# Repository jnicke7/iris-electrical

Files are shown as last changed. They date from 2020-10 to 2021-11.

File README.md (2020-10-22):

# iris-electrical

IRIS Electrical Team Arduino Code Repository

## void setup()

First code run by Arduino on start

Sets up serial inputs for the sabertooth from the Odroid

Assigns the direct and pwm pins as outputs to the LACs

## void loop()

Runs after setup

Creates the checksum to make sure that the data is being passed through to the Arduino correctly

Uses largestOneIndex helper function to calculate

CRC: Cyclic Redundancy Check

If the checksum came out incorrect then it will ignore the instruction.

### Motor ID Values:

    0: Left Drive
    1: Right Drive
    2: Bucket Ladder M
    3: Dump Conveyor LA
    4: Bucket Ladder LA
    5: Agitator
    6: Dump Conveyor M
    7: Shuts off all motors

Based on the motor ID value it will call the sabertooth or the linear actuators

## void linac(int power, int motor)

Inputs: power number and the specific motor number

Outputs: direction and power specific to a motor

Creates changes with two functions:

### digitalWrite(dir\_1, (int)(OdroidIn[1]/128));

Sets the direction of a given motor

### analogWrite(pwm\_3, power\*2);

Sets the magnitude of the given motor

## void stop()

This function runs through each motor and reduces its speed to 0

## int largestOneIndex(unsignedint curr)

This function parses through curr bitwise to find the index of the most significant '1'

Inputs: curr, 16-bit chars

Outputs: integer i, the first index of '1'

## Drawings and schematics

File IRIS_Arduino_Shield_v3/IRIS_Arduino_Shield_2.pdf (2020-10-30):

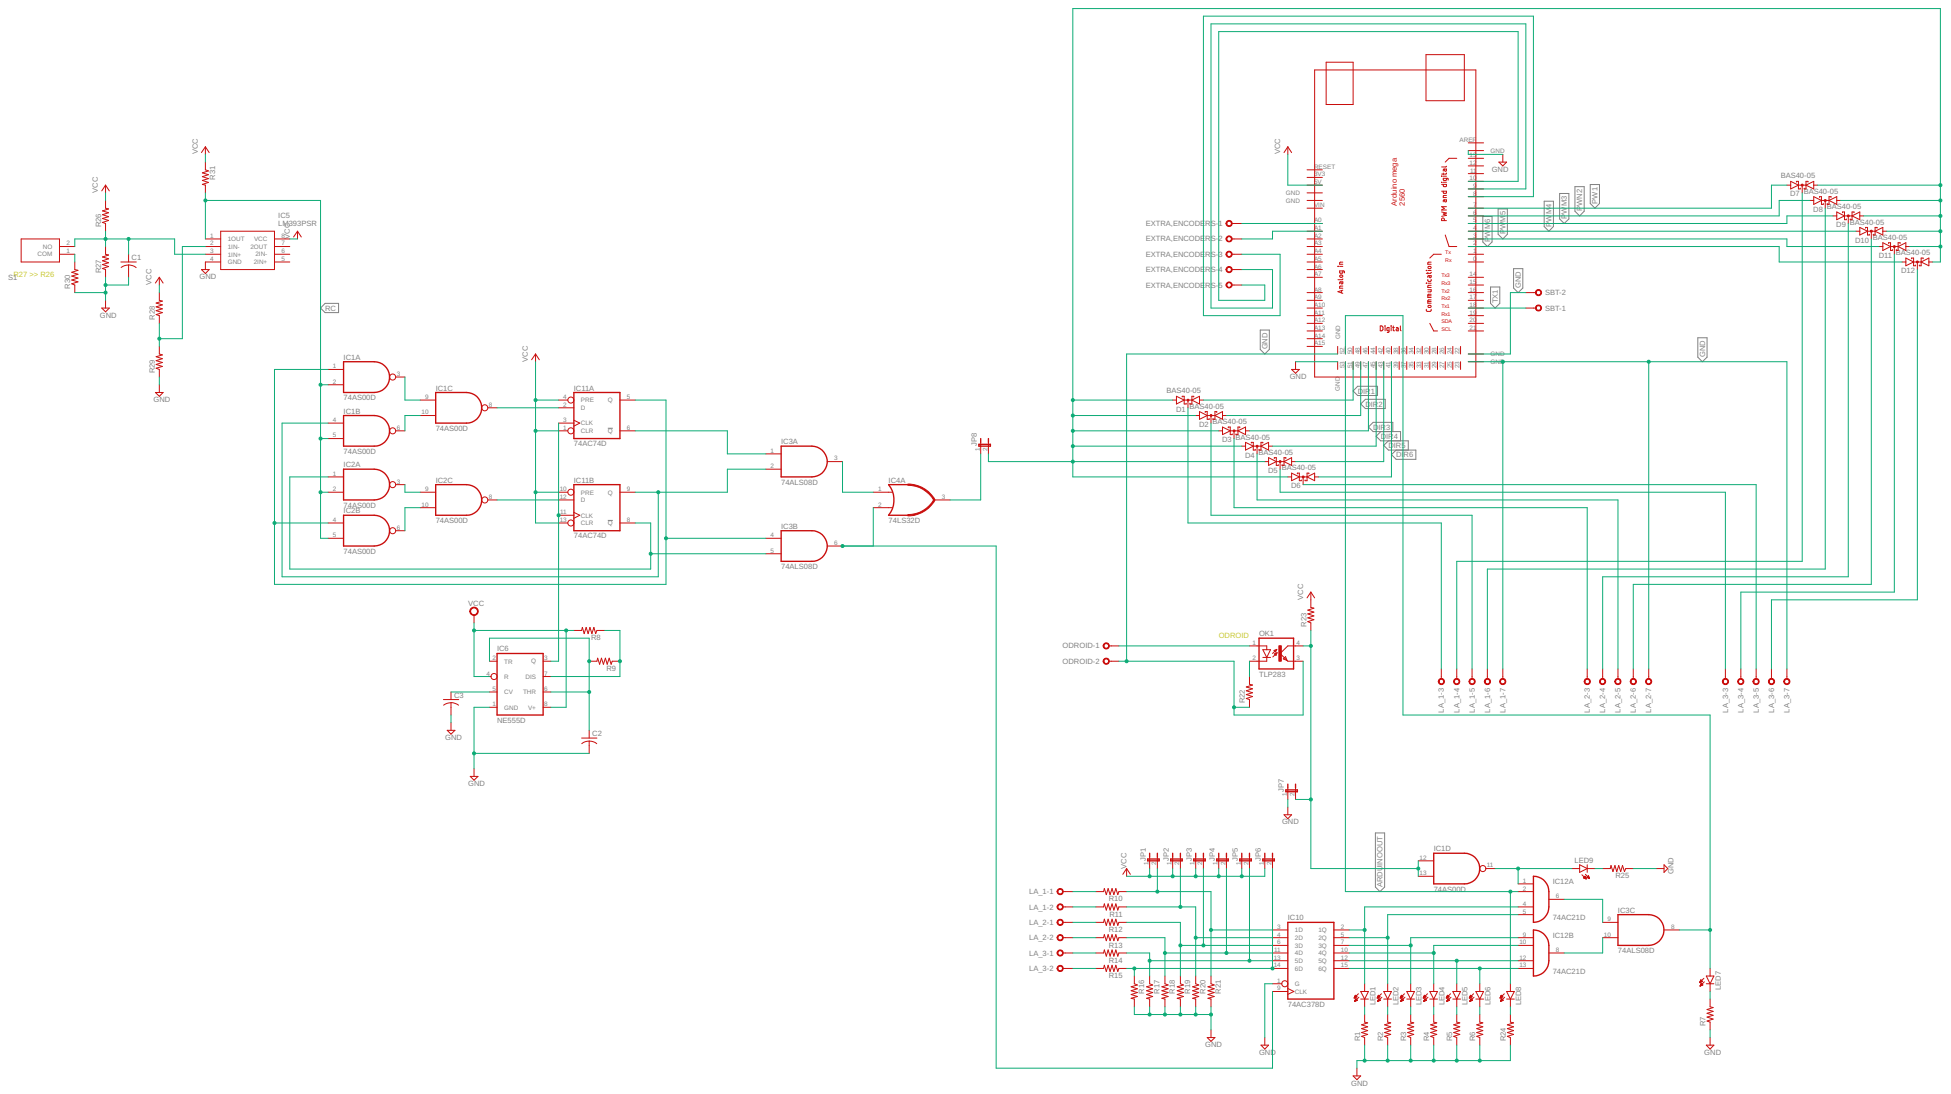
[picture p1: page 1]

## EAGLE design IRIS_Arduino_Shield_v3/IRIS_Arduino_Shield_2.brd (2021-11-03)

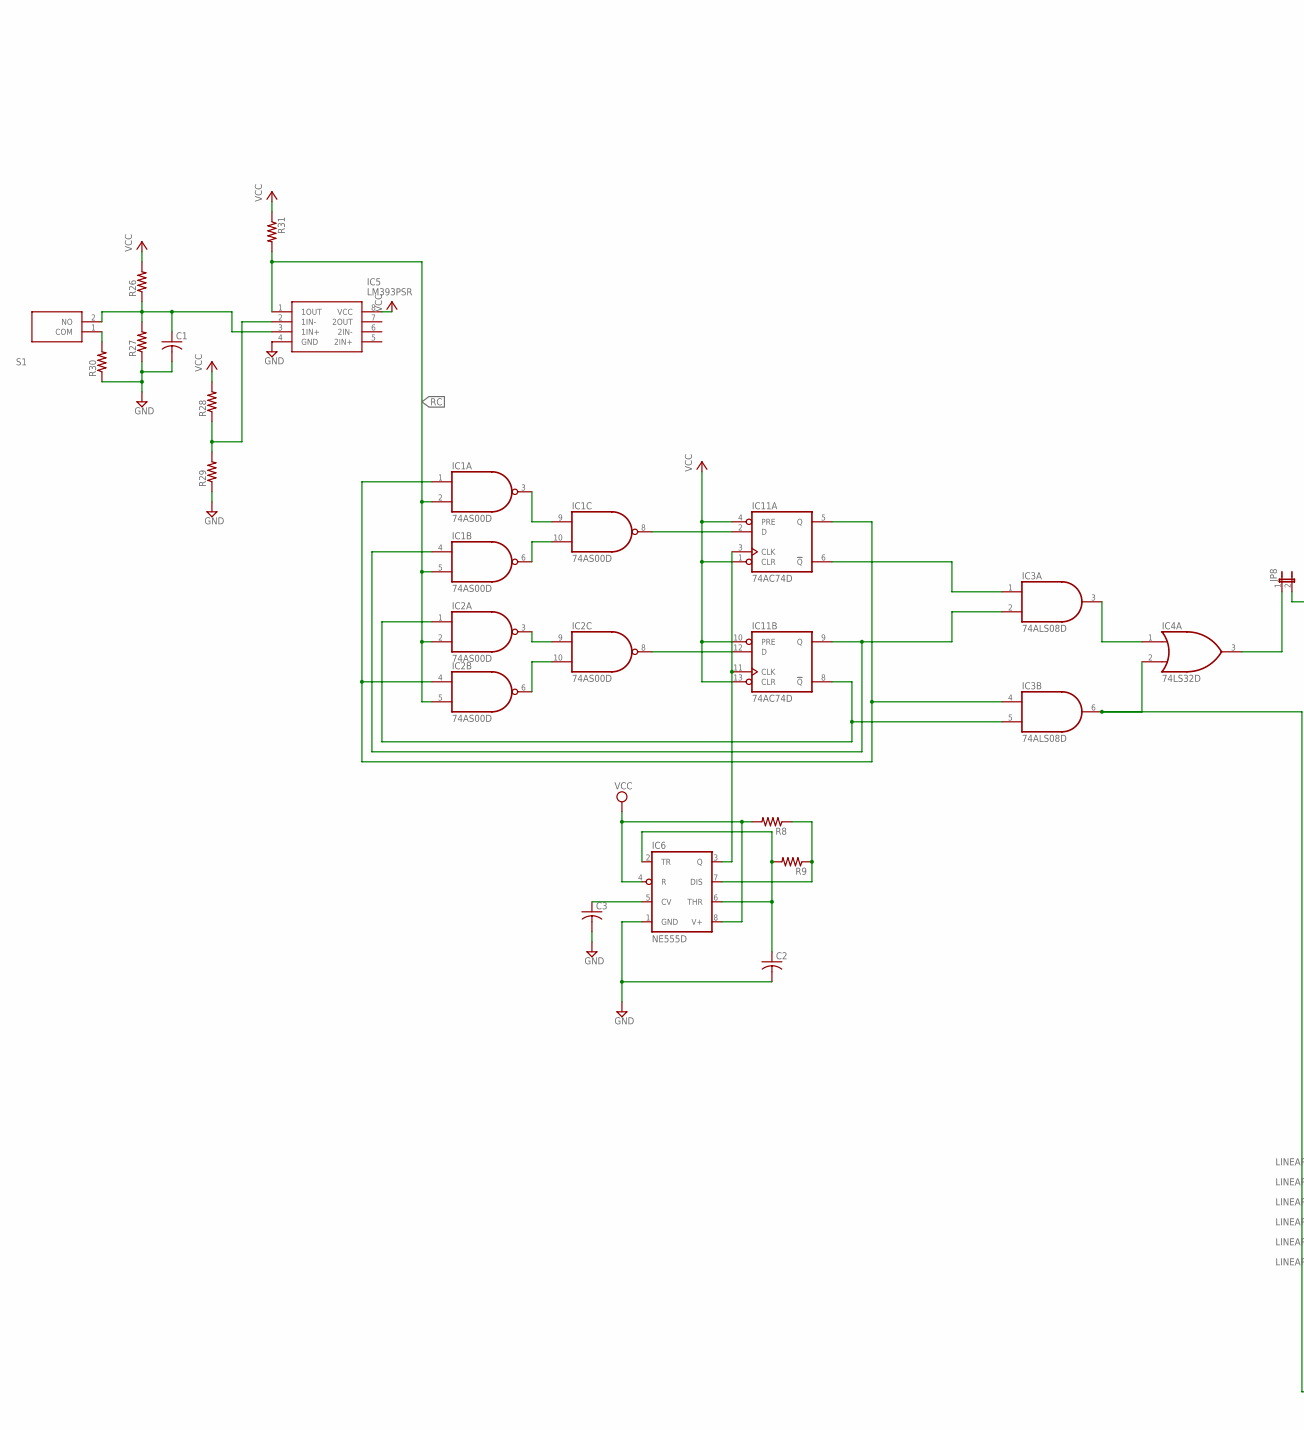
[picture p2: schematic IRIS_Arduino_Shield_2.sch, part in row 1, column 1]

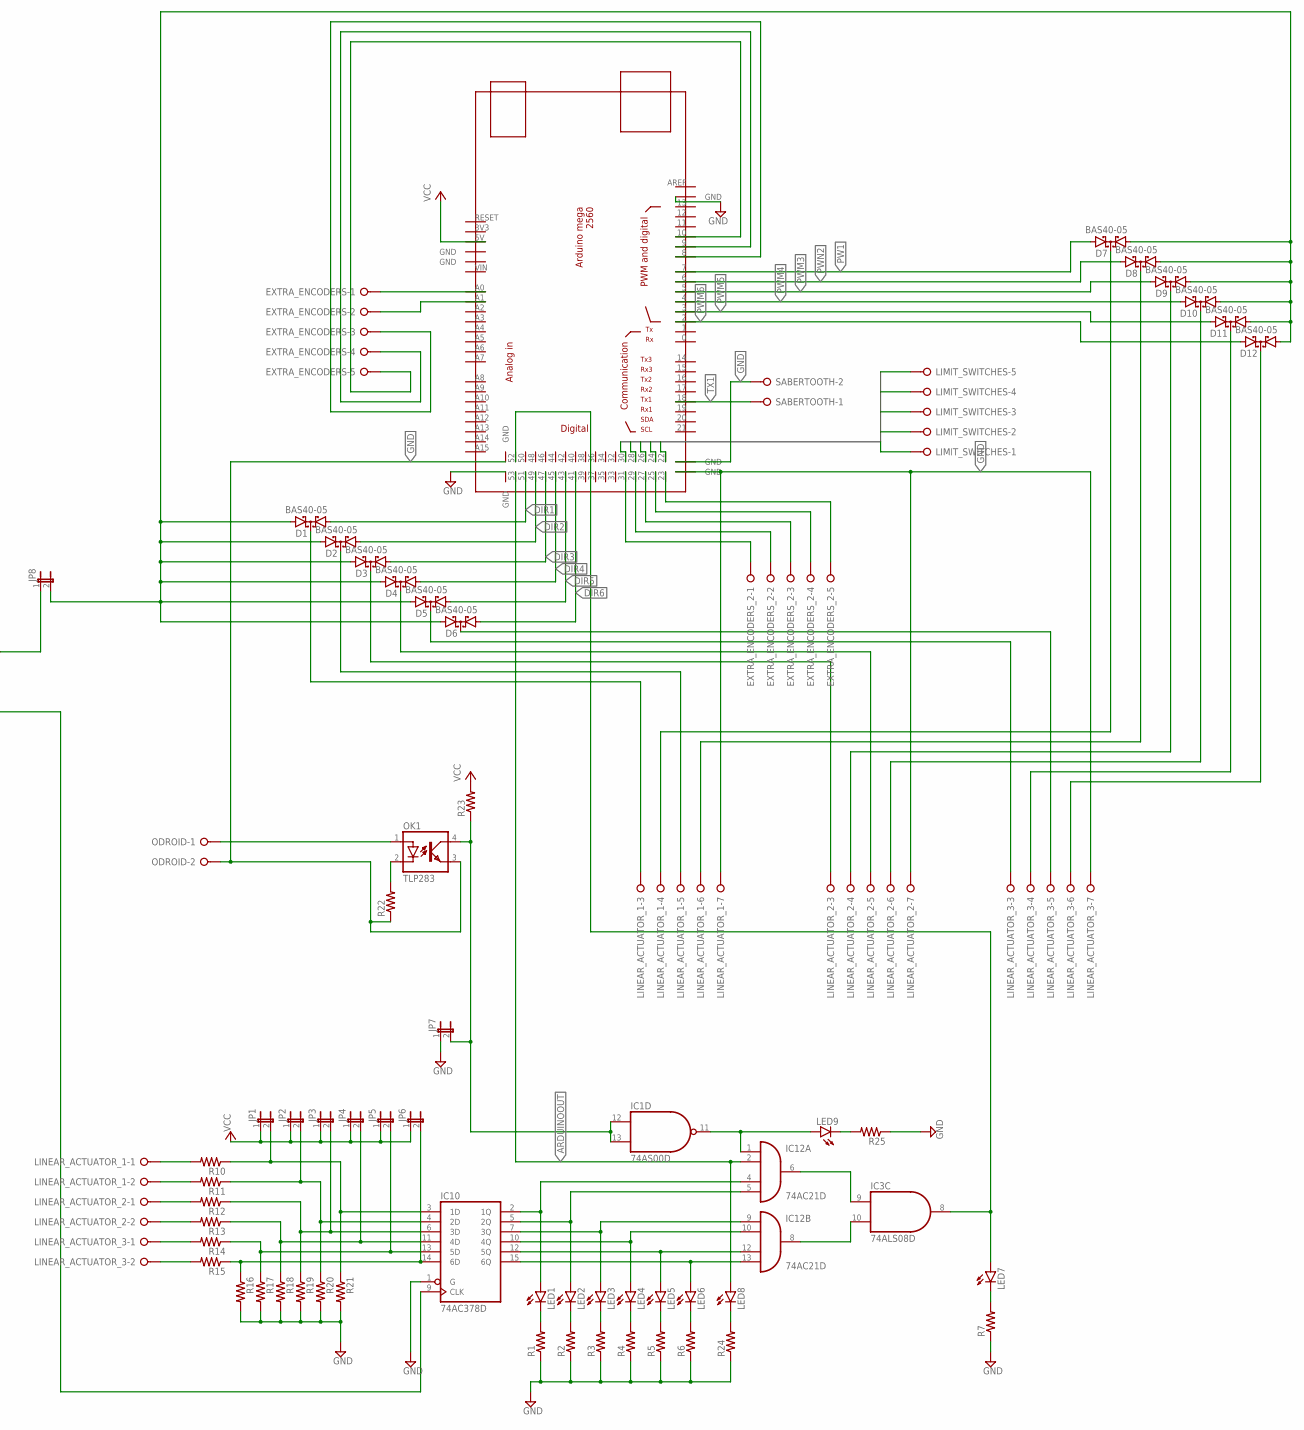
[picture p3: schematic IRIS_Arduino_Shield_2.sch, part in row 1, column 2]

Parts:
C1, C2, C3: C-USC0805; C0805
D1, D2, D3, D4, D5, D6, D7, D8, D9, D10, D11, D12: BAS40-05; SOT23
EXTRA_ENCODERS: W237-05P; W237-5P
EXTRA_ENCODERS_2: W237-05P; W237-5P
IC1, IC2: 74AS00D; SO14
IC3: 74ALS08D; SO14
IC4: 74LS32D; SO14
IC5: LM393PSR; SOIC127P780X200-8N
IC6: NE555D; SO08
IC10: 74AC378D; SO16
IC11: 74AC74D; SO14
IC12: 74AC21D; SO14
JP1, JP2, JP3, JP4, JP5, JP6, JP7, JP8: JP1E; JP1
LED1, LED2, LED3, LED4, LED5, LED6, LED7, LED8, LED9: LEDCHIPLED_1206; CHIPLED_1206
LIMIT_SWITCHES: W237-05P; W237-5P
LINEAR_ACTUATOR_1, LINEAR_ACTUATOR_2, LINEAR_ACTUATOR_3: W237-07P; W237-7P
ODROID: W237-02P; W237-132
OK1: TLP283; MINI-FLAT-4
R1, R2, R3, R4, R5, R6, R7, R8, R9, R10, R11, R12, R13, R14, R15, R16, R17, R18, R19, R20, R21, R22, R23, R24, R25, R26, R27, R28, R29, R30, R31: R-US_R0805; R0805
S1: PTS636_SL43_SMTR_LFS; PTS636SL43SMTRLFS
SABERTOOTH: W237-02P; W237-132
U$1: MEGA_DEVICE; MEGAOUTLINE

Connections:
ARDUINOOUT: IC12.2 (I1), LED8.A, U$1.53
DIR1: D1.1 (A1), U$1.51
DIR2: D2.1 (A1), U$1.49
DIR3: D3.1 (A1), U$1.47
DIR4: D4.1 (A1), U$1.45
DIR5: D5.1 (A1), U$1.43
DIR6: D6.1 (A1), U$1.41
GND: C1.2, C2.2, C3.2, IC1.7 (GND), IC2.7 (GND), IC3.7 (GND), IC4.7 (GND), IC5.4 (GND), IC6.1 (GND), IC10.1 (G), IC10.8 (GND), IC11.7 (GND), IC12.7 (GND), JP7.1, LINEAR_ACTUATOR_1.7, LINEAR_ACTUATOR_2.7, LINEAR_ACTUATOR_3.7, ODROID.2, OK1.3 (EMIT), R1.1, R2.1, R3.1, R4.1, R5.1, R6.1, R7.1, R16.2, R17.2, R18.2, R19.2, R20.2, R21.2, R22.1, R24.1, R25.1, R27.1, R29.1, R30.1, SABERTOOTH.2, U$1.GND@1 (GND), U$1.GND@4 (GND), U$1.GND@5 (GND), U$1.GND@6 (GND), U$1.GND@7 (GND)
LA_TEST: D1.2 (A2), D2.2 (A2), D3.2 (A2), D4.2 (A2), D5.2 (A2), D6.2 (A2), D7.1 (A1), D8.1 (A1), D9.1 (A1), D10.1 (A1), D11.1 (A1), D12.1 (A1), JP8.2
unnamed: IC1.3 (O), IC1.9 (I0)
unnamed: IC1.6 (O), IC1.10 (I1)
unnamed: IC1.8 (O), IC11.2 (D)
unnamed: D7.3 (C), LINEAR_ACTUATOR_1.4
unnamed: IC6.3 (Q), IC11.3 (CLK), IC11.11 (CLK)
unnamed: IC2.8 (O), IC11.12 (D)
unnamed: LED1.C, R1.2
unnamed: LED2.C, R2.2
unnamed: LED3.C, R3.2
unnamed: LED4.C, R4.2
unnamed: LED5.C, R5.2
unnamed: LED6.C, R6.2
unnamed: IC10.2 (1Q), IC12.4 (I2), LED1.A
unnamed: IC10.5 (2Q), IC12.5 (I3), LED2.A
unnamed: IC10.7 (3Q), IC12.9 (I0), LED3.A
unnamed: IC10.10 (4Q), IC12.10 (I1), LED4.A
unnamed: IC10.12 (5Q), IC12.12 (I2), LED5.A
unnamed: IC10.15 (6Q), IC12.13 (I3), LED6.A
unnamed: IC3.9 (I0), IC12.6 (O)
unnamed: IC3.10 (I1), IC12.8 (O)
unnamed: IC3.8 (O), LED7.A, U$1.52
unnamed: LED7.C, R7.2
unnamed: IC2.3 (O), IC2.9 (I0)
unnamed: IC2.6 (O), IC2.10 (I1)
unnamed: IC4.3 (O), JP8.1
unnamed: C1.1, IC5.3 (1IN+), R26.1, R27.2, S1.2 (NO)
unnamed: IC5.2 (1IN-), R28.1, R29.2
unnamed: C2.1, IC6.2 (TR), IC6.6 (THR), R9.2
unnamed: D1.3 (C), LINEAR_ACTUATOR_1.3
unnamed: IC6.7 (DIS), R8.1, R9.1
unnamed: IC3.1 (I0), IC11.6 (!Q)
unnamed: IC10.3 (1D), JP1.2, R10.1, R21.1
unnamed: ODROID.1, OK1.1 (A)
unnamed: IC10.4 (2D), JP2.2, R11.1, R20.1
unnamed: IC10.6 (3D), JP3.2, R12.1, R19.1
unnamed: IC10.11 (4D), JP4.2, R13.1, R18.1
unnamed: IC10.13 (5D), JP5.2, R14.1, R17.1
unnamed: IC10.14 (6D), JP6.2, R15.1, R16.1
unnamed: D8.3 (C), LINEAR_ACTUATOR_1.6
unnamed: D9.3 (C), LINEAR_ACTUATOR_2.4
unnamed: IC2.1 (I0), IC3.5 (I1), IC11.8 (!Q)
unnamed: IC1.1 (I0), IC2.4 (I0), IC3.4 (I0), IC11.5 (Q)
unnamed: IC1.4 (I0), IC3.2 (I1), IC11.9 (Q)
unnamed: D10.3 (C), LINEAR_ACTUATOR_2.6
unnamed: D11.3 (C), LINEAR_ACTUATOR_3.4
unnamed: LED8.C, R24.2
unnamed: OK1.2 (C), R22.2
unnamed: LED9.C, R25.2
unnamed: IC1.12 (I0), IC1.13 (I1), JP7.2, OK1.4 (COL), R23.1
unnamed: EXTRA_ENCODERS.1, U$1.A0
unnamed: IC1.11 (O), IC12.1 (I0), LED9.A
unnamed: EXTRA_ENCODERS.2, U$1.A1
unnamed: EXTRA_ENCODERS.4, U$1.9
unnamed: R30.2, S1.1 (COM)
unnamed: D2.3 (C), LINEAR_ACTUATOR_1.5
unnamed: EXTRA_ENCODERS.3, U$1.8
unnamed: D3.3 (C), LINEAR_ACTUATOR_2.3
unnamed: D4.3 (C), LINEAR_ACTUATOR_2.5
unnamed: D5.3 (C), LINEAR_ACTUATOR_3.3
unnamed: D6.3 (C), LINEAR_ACTUATOR_3.5
unnamed: D12.3 (C), LINEAR_ACTUATOR_3.6
unnamed: IC3.6 (O), IC4.2 (I1), IC10.9 (CLK)
unnamed: LINEAR_ACTUATOR_1.1, R10.2
unnamed: LINEAR_ACTUATOR_1.2, R11.2
unnamed: LINEAR_ACTUATOR_2.1, R12.2
unnamed: LINEAR_ACTUATOR_2.2, R13.2
unnamed: LINEAR_ACTUATOR_3.1, R14.2
unnamed: LINEAR_ACTUATOR_3.2, R15.2
unnamed: C3.1, IC6.5 (CV)
unnamed: EXTRA_ENCODERS.5, U$1.10
unnamed: IC3.3 (O), IC4.1 (I0)
unnamed: EXTRA_ENCODERS_2.5, U$1.23
unnamed: EXTRA_ENCODERS_2.4, U$1.25
unnamed: EXTRA_ENCODERS_2.3, U$1.27
unnamed: EXTRA_ENCODERS_2.2, U$1.29
unnamed: EXTRA_ENCODERS_2.1, U$1.31
unnamed: LIMIT_SWITCHES.1, U$1.30
unnamed: LIMIT_SWITCHES.2, U$1.28
unnamed: LIMIT_SWITCHES.3, U$1.26
unnamed: LIMIT_SWITCHES.4, U$1.24
unnamed: LIMIT_SWITCHES.5, U$1.22
PW1: D7.2 (A2), U$1.7
PWM3: D9.2 (A2), U$1.5
PWM4: D10.2 (A2), U$1.4
PWM5: D11.2 (A2), U$1.3
PWM6: D12.2 (A2), U$1.2
PWN2: D8.2 (A2), U$1.6
RC: IC1.2 (I1), IC1.5 (I1), IC2.2 (I1), IC2.5 (I1), IC5.1 (1OUT), R31.2
TX1: SABERTOOTH.1, U$1.18
VCC: IC1.14 (VCC), IC2.14 (VCC), IC3.14 (VCC), IC4.14 (VCC), IC5.8 (VCC), IC6.4 (R), IC6.8 (V+), IC10.16 (VCC), IC11.1 (CLR), IC11.4 (PRE), IC11.10 (PRE), IC11.13 (CLR), IC11.14 (VCC), IC12.14 (VCC), JP1.1, JP2.1, JP3.1, JP4.1, JP5.1, JP6.1, R8.2, R23.2, R26.2, R28.2, R31.1, U$1.5V

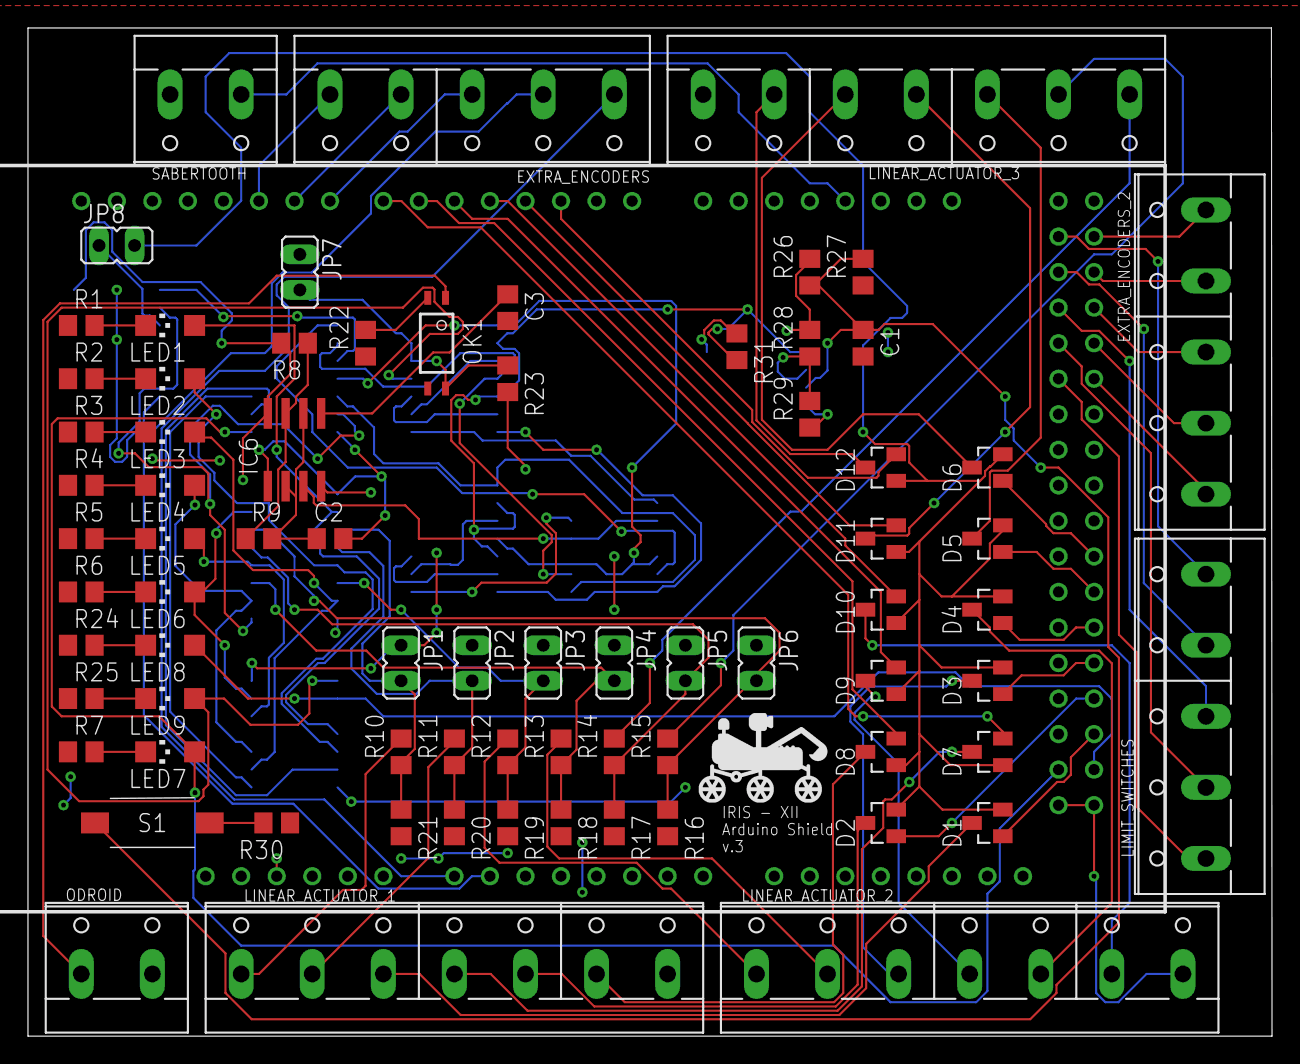
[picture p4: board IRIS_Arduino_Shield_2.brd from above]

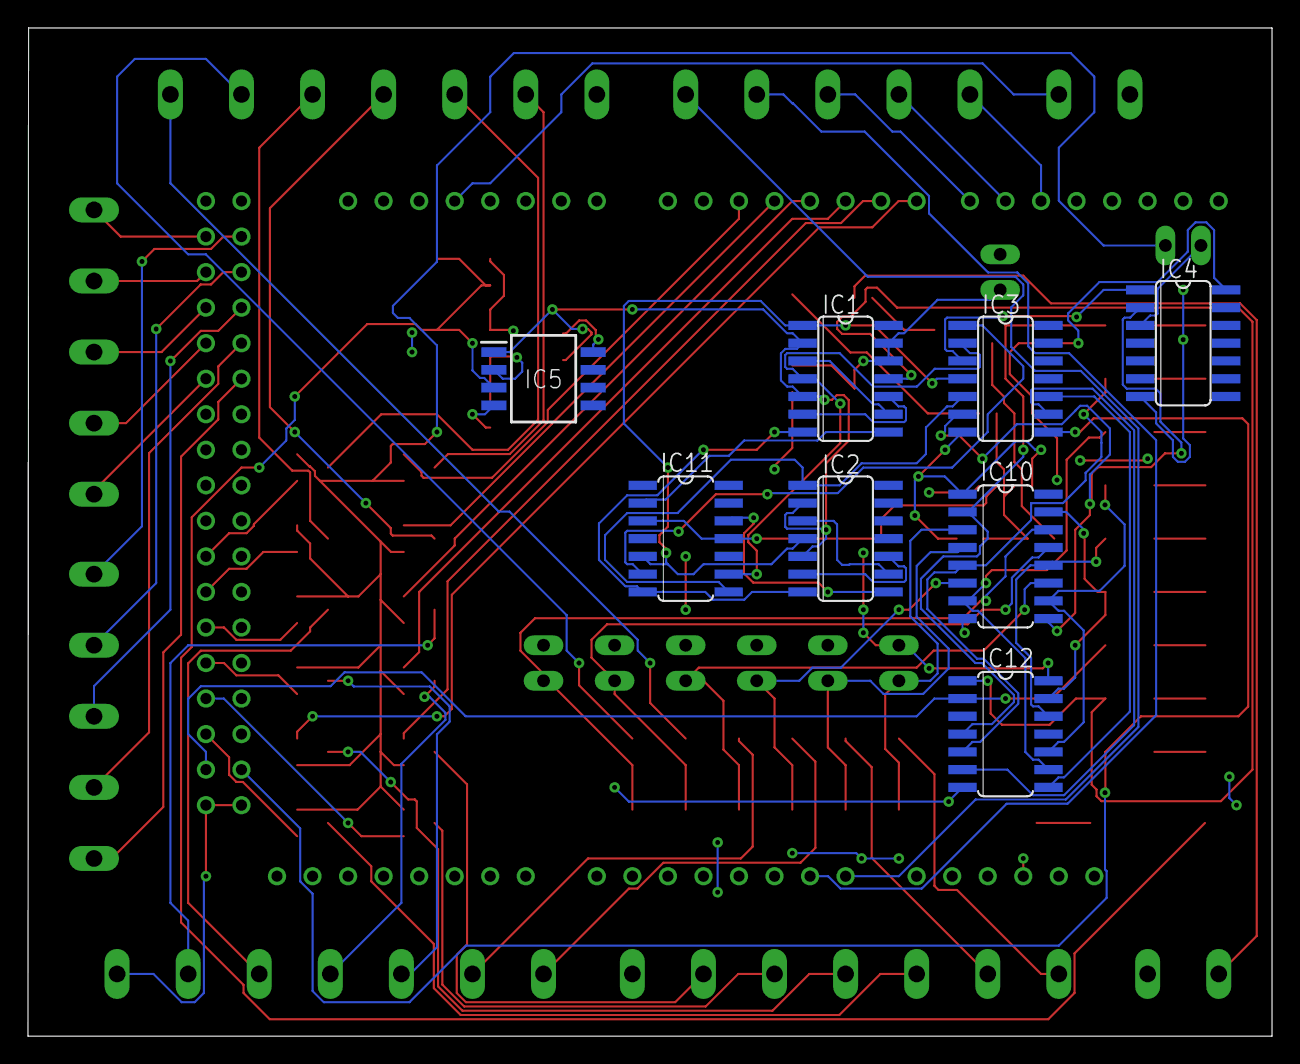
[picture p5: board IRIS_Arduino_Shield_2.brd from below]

Board: 2 copper layers, 88.9 x 72.1 mm, 83 parts (8 on the bottom side), 99 nets.

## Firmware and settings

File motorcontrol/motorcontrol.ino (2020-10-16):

#include <Sabertooth.h>

Sabertooth ST[2] = { Sabertooth(128,Serial1), Sabertooth(129,Serial1) }; //128 ->Left and right Drive, 129->Bucket Ladder

#define dir_1 22
#define pwm_1 2
#define dir_2 23
#define pwm_2 3

#define dir_3 24
#define pwm_3 4
#define dir_4 25
#define pwm_4 5




void setup()
{
  SabertoothTXPinSerial.begin(9600);
  Sabertooth::autobaud(SabertoothTXPinSerial);

  Serial.begin(9600); //serial input from Odroid.
  

pinMode(pwm_1,OUTPUT);
pinMode(dir_1,OUTPUT);
pinMode(pwm_2,OUTPUT);
pinMode(dir_2,OUTPUT);

pinMode(pwm_3,OUTPUT);
pinMode(dir_3,OUTPUT);
pinMode(pwm_4,OUTPUT);
pinMode(dir_4,OUTPUT);


}

void loop()
{

   byte OdroidIn[2];
   
  Serial.readBytes(OdroidIn,2); 
   unsigned int OdroidInInt = OdroidIn[1]+OdroidIn[0]*256;
   unsigned int CRC = 18;
   unsigned int msg = OdroidInInt % 2048;
   unsigned int checksum = OdroidInInt / 2048;
   unsigned int curr = msg*32 + checksum;

   int a, index;
   while (curr >= 32) {
    index = largestOneIndex(curr);
    a = CRC << (index - 5);
    curr ^= a;
   }
   if (curr) {
    // CRC came back bad
    // do some error handling here??
    return;
   }
   
  //First byte: contains motorVal and checksum, in the Order Checksum:[4:0],motorVal[2:0]
  //Second byte: is the power value.
  /*
   * Input[0],[1],[2] correspond to motor
  KEY:
  Motor ID: 
0: Left Drive
1: Right Drive
2: Bucket Ladder M
3: dump conveyor LA
4: bucket ladder LA
5: agitator
6: dump conveyor M
7: stops motors
  */
  int motorVal = OdroidIn[0] % 8; 
  int power = OdroidIn[1] %128;
    if(OdroidIn[1]/128 == 1 && motorVal<3){
      power*=-1;
    }
    if(motorVal == 7){
      Stop();
      } 
  else if(motorVal<3){ //call a sabertooth for the action
    ST[(motorVal%4)/2].motor(motorVal%2+1,power);
    }
  else{//call a linAC
    linAC(power,motorVal);
    }
 
}

 void linAC(int power, int motor){
    switch(motor) {

   case 3 :
      digitalWrite(dir_1, (int)(OdroidIn[1]/128)); //controls the direction the motor;
      analogWrite(pwm_1, power*2); 
      break; 
   case 4 :
      digitalWrite(dir_2, (int)(OdroidIn[1]/128)); //controls the direction the motor;
      analogWrite(pwm_2, power*2);
      break; 
  case 5 :
      digitalWrite(dir_3, (int)(OdroidIn[1]/128)); //controls the direction the motor;
      analogWrite(pwm_3, power*2);
      break; /
  
   case 6 :
      digitalWrite(dir_4, (int)(OdroidIn[1]/128)); //controls the direction the motor;
      analogWrite(pwm_4, power*2);
      break;  
  
  default : 
   return;
}
  
  }
void Stop(){
  for(int i = 3; i<7; i++){
    linAC(0,i);
    }
  ST[0].stop();
  ST[1].stop();
  
  }

int largestOneIndex(unsigned int curr) {
  int i = 15;
  while (i >= 0) {
    if (curr & (1 << i)) {
      break;
    }
    i--;
  }
  return i;
}

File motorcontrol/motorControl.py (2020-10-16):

#use pip3 install pyserial
import serial

def writeMotor(ser, motorID, dir, speed):
    ser.flushInput()
    # calculate cmd word based on motorID, dir, and speed
    # calculate CRC based on cmd word
    cmd = # TODO [4:0]CRC, [2:0]motorID, [0]dir, [6:0]speed
    val = bytes(str(cmd), 'utf-8')
    ser.write(val)


if (__name__ == "__main__"):
    ser = serial.Serial("/dev/ttyACM0", 9600)
    input = input("[motorId] [dir] [speed]: ")
    motorID = #some test code
    dir = #some test code
    speed = #some test code
    writeMotor(ser, motorID, dir, speed)

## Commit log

2020-10-07 Added motorcontrol.ino
2020-10-08 10/7
    Added arduino code for Sabertooth/linAC, and added sabertooth library
2020-10-15 Pushing motor control loop changes
2020-10-15 Algorithm checking and rework for bytewise input
    [motorcontrol.ino]
2020-10-30 Added EAGLE files
    [555 timer.sch, IRIS_Arduino_Shield_2.brd, IRIS_Arduino_Shield_2.sch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]
2021-11-03 Added board v3
    [555 timer.sch, IRIS_Arduino_Shield_2.brd, IRIS_Arduino_Shield_2.sch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]
